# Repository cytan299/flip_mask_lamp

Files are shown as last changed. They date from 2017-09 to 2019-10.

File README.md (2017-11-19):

# Remote controlled flip Bahtinov mask and lamp

by C.Y. Tan 2017

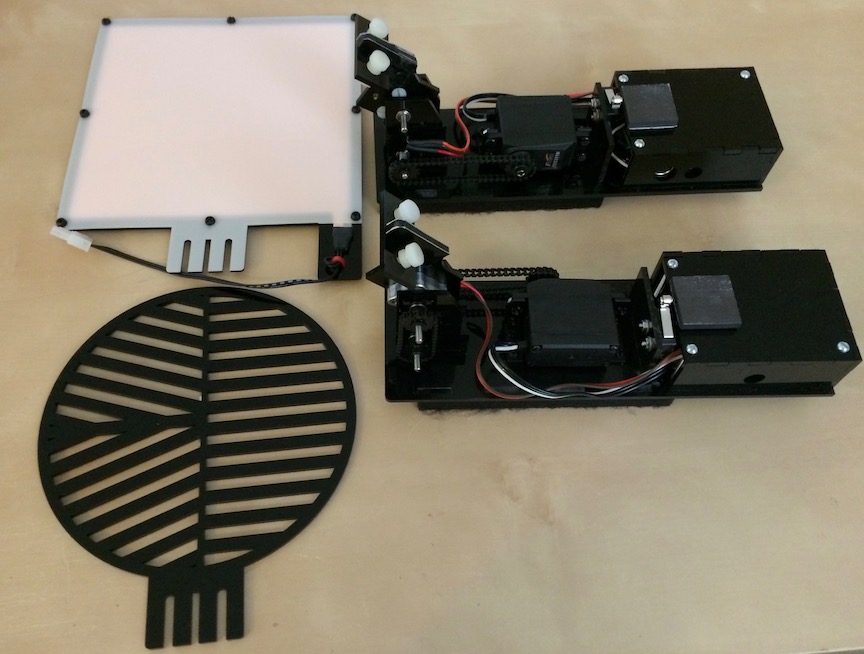
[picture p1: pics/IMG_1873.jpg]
Flip mask and lamp


I made a flip mask and lamp for my FSQ106 so that when they are
mounted on the telescope, they will balance each other out when mounted on
the opposite side of the telescope.

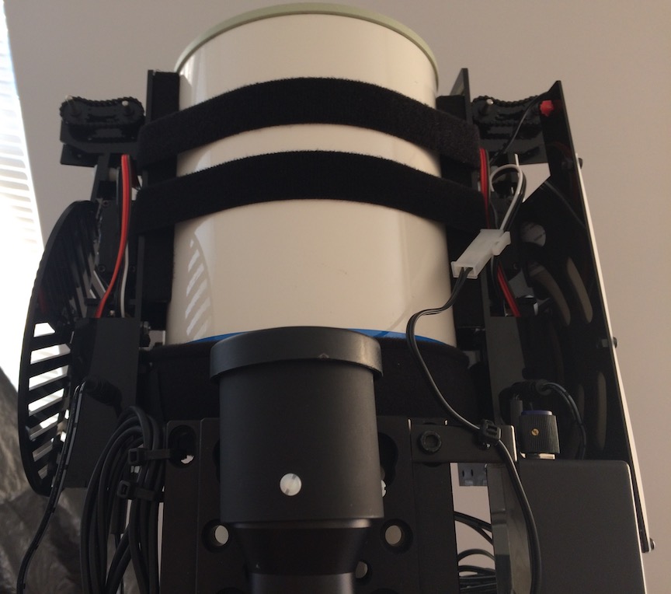
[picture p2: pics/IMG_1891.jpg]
Flip mask and lamp mounted on an FSQ106


## Design

The flip mask and lamp are designed as a master and slave pair. I have
chosen the flip mask controller to be the master and the flip lamp
controller to be the slave.

The mechanical design of the flip mask and lamp are mirror images of
each other. The principal parts used in the design are as follows:

* A servo controller made by Pololu called the [Maestro](https://www.pololu.com/product/1350).
* A servo that rotates greater than 270
degrees: the [Feetech FR5311M](http://www.feetechrc.com/product/continuous-rotation-servo/two-working-mode-digital-programmable-metal-gears-servo-fr5311m/).
* A [sprocket and chain system](https://www.servocity.com/0-1227-pitch-nylon-servo-sprockets) for connecting the servo to the mask and lamp.
* Interlock switches to indicate where the mask or lamp is
  * A mechanical lever switch
  * A Hall switch
* A lamp made from an
[electroluminescent panel with dimmer and power inverter](https://knema.com/collections/electroluminescent-el-panels/products/electroluminescent-panel-split-electrode-type-blue-green-or-white-includes-power-supply-and-dimmi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).
* Filter sheets have been added so that the RGB components of the EL panel have nearly
  the same intensities.

## Movie

A movie of how the flip mask and lamp in action can be found on [youtube](https://youtu.be/KrSrh4rIldk).

## Support

This is unsupported hardware. Build at your own peril! :)

You can submit questions or bug reports using the
[issues](https://github.com/cytan299/flip_mask_lamp/issues) tab on
the right and then click on **NEW**.

Have fun!

## Directory structure

* **howto** Assembly instructions for the flip mask and lamp.
* **ponoko** The files that are used for laser cutting the acrylic parts of
the design. These files can be sent directly to
[Ponoko](http://www.ponoko.com) for laser cutting.
* **bom** Bill of materials for 1 pair of flip mask and lamp.
* **eagle** Eagle schematic and board files.
* **python** Source code for the python control program.
* **pics** Photographs used in the README's and Wiki.

## Other information

More information can be found in he *README.md* files in each
directory and the [wiki](https://github.com/cytan299/flip_mask_lamp/wiki/Flip-Mask-and-Lamp) of this project on github.

## Copyright
All the software, documentation, and hardware that I have written is
copyright 2017 C.Y. Tan.

All software is released under GPLv3

All documentation is released under Creative Commons
Attribution-ShareAlike 3.0 Unported License or GNU Free
Documentation License, Version 1.3

All hardware is released under CERN Hardware Open License v1.2

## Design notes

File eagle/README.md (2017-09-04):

# Eagle files

These are the eagle files that can be sent to pc board manufacturers to
be made. There is a free version of [eagle](http://cadsoftusa.com)
that can be downloaded to view the designs.

## Directories

* **flip_mask** The flip mask control unit. This unit 
  * controls the Bahtinov mask
  * is the master that controls the flip lamp unit that is the slave unit
  * contains the USB interface
  * has the [Maestro](https://www.pololu.com/product/1350) servo controller
* **flip_lamp** The flip lamp control unit. This unit
  * controls the lamp

## Copyright

The schematic and board designs are copyright 2017 C.Y. Tan and
released under the CERN Open Hardware License v1.2

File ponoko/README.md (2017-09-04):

# Flip mask and lamp plastic parts

The flip mask and lamp plastic parts are in this directory. Note that
the svg files are *not* empty! The lines are 0.01 mm thick that are
required for laser cutting by [Ponoko](http://www.ponoko.com). To see
the designs, either zoom in or change the thickness of the lines with
a programme like [Inkscape](https://inkscape.org/en/).

* *flip_mask_and_lamp_ponoko_v2a.svg* contains enough parts for one pair
of flip mask and lamp parts. The remaining parts are sufficient for
either one flip mask or slave. The specified material used for manufacture at [Ponoko](http://www.ponoko.com) is
  * Black acrylic
  * 3.0 mm thick
  * P2 - 384.0 mm long x 384.0 mm wide
* *flip_lamp_front_ponoko_v2.svg* contains the design for the front of the lamp. The
material used is
  * White Delrin
  * 0.8 mm thick
  * P2 - 384.0 mm long x 384.0 mm wide
* *flip_lamp_back_ponoko_v2.svg*  contains the design for the back of the lamp. The
material used is
  * Black acrylic
  * 1.5 mm thick
  * P2 - 384.0 mm long x 384.0 mm wide

## Copyright

The flip mask and lamp design is copyright 2017 C.Y. Tan and released under the CERN Open Hardware License v1.2

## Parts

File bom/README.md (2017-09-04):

# Bill of Materials

The estimated cost for building *one* pair of flip mask and lamp is
about $400. Taxes and shipping have not been included. This is the
lower bound for the cost of one such device because, in practise, it
is not possible to just buy 1 screw.  The bom.ods file is readable
using [LibreOffice Calc](http://www.libreoffice.org).

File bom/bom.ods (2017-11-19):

Part # | Description | Price each | # required | Cost of 1 | Bought from | Total cost of 1
FR5311M | Digital Servo | $18.76 | 2 | $37.52 | www.robotshop.com | $417.71
RB-Fit-24 | Feetech FRS servo programmer | $4.99 | 1 | $4.99 | www.robotshop.com
RB-lyn-79 | Lynxmotion EZ aluminum servo mount | $8.95 | 1 | $8.95
C1227 | 1 foot 0.1227 plastic chain | $7.49 | 2 | $14.98 | www.servocity.com
FS154 | 15T, 25 spline servo teeth | $3.99 | 2 | $7.98
S152 | 15T press fit sprocket | $2.27 | 6 | $13.62
535036 | 1/8” ID, 1/4” OD flanged ball bearing | $1.40 | 8 | $11.16
634116 | 1/8” SS precision shafting 2” | $0.49 | 4 | $1.96
ROB-09664 | Micro Maestro 6-channel | $19.95 | 1 | $19.95 | www.sparkfun.com
ROB-12108 | Set screw hub – 1/8” bore | $4.99 | 2 | $9.98
EL8006 | Parallel electrode 6”x6” dimming EL panel with dimming controller and PS | $69.25 | 1 | $69.25 | www.knema.com
102-2705-ND | DCDC converter CUINC P7805-Q24-S5 | $4.94 | 1 | $4.94 | www.digikey.com
2144690 | 2.1 mm PCB mount power jack | $0.69 | 5 | $3.45
138202 | 0.0047uF, 50V cap | $0.15 | 2 | $0.30
1583041 | Solid state relay LCA710 | $4.49 | 1 | $4.49
46341 | 74LS05 | $0.79 | 1 | $0.79
119475 | 6 pin mini DIN socket female | $0.89 | 2 | $1.78
100766 | Female contact crimp pin | $0.19 | 12 | $2.28
303562 | Mini-fit female 2 position receptacle | $0.25 | 1 | $0.25
881004 | Mini-fit vertical male 2 position receptacle | $0.25 | 1 | $0.25
401824 | Mini-fit male contacts | $0.09 | 2 | $0.18
401701 | Mini-fit female contacts | $0.09 | 2 | $0.18
2096763 | 2.1 mm with 6 ft pigtail | $1.95 | 3 | $5.85
100280 | 24 awg 2 strand 100 ft | $9.95 | 0.03 | $0.30
2230352 | 14 pin IC socket | $0.49 | 1 | $0.49
167004 | 6 pin IC socket | $0.39 | 1 | $0.39
159599 | Roller action subminature switch | $1.35 | 2 | $2.70
158 | Hall effect sensor US5881LUA | $2.00 | 2 | $4.00 | www.adafruit.com
3141 | Female/female jumper wires | $2.95 | 1 | $2.95
3145 | Single row wire housing pack | $1.95 | 0.2 | $0.39
flip mask PCB | flip mask PCB | $8.67 | 1 | $8.67 | www.oshpark.com
flip lamp PCB | flip lamp PCB | $6.00 | 0 | $0.00
flip lamp PCB v2 | flip lamp PCB v2 | $6.00 | 1 | $6.00
308938 | flip mask, flip lamp front, flip lamp back | $95.76 | 1 | $95.76 | www.ponoko.com
30699202874 | Corner brace 1.5” black | $0.75 | 2 | $1.49 | www.homedepot.com
887480029215 | Machine screws and nuts 2-56 1/2” | $0.15 | 4 | $0.59
30699370115 | Machine screws and nuts 2-56 3/8” | $0.15 | 2 | $0.30
887480029215 | Machine screws and nuts 6-32 3/8” | $0.15 | 8 | $1.18
887480029918 | Machine screws and nuts 4-40 1.5” | $0.30 | 6 | $1.77
75967907006 | 7/8”*23 velcro straps | $1.32 | 2 | $2.65
302370993711 | 3ft DIN6 M to M cable | $1.99 | 1 | $1.99 | PJAJ Inc (ebay)
B01EIY7YKW | 150 M2-M5 nylon screws + nuts | $4.76 | 1 | $4.76 | Sodial® (amazon.com)
 | 160 M3 8 sizes nylon screws + nuts | $8.99 | 1 | $8.99 | GoChange (amazon.com)
147777 | Soft bendable aluminium tubes (3/32,1/8, 5/32) | $2.32 | 1 | $2.32 | www.hobbylobby.com
1025816 | Plast-I-weld | $7.99 | 1 | $7.99
 | Craft power magnets | $5.99 | 0 | $0.00
 | Square magnets with foam adhesive | $0.37 | 2 | $0.75
 | Galvanized steel sheet | $3.99 | 1 | $3.99
 | Black felt sheet | $3.99 | 1 | $3.99
D12-N52 | 1/16” dia x 1/8” thick magnet | $0.14 | 2 | $0.28 | www.kjmagnetics.com (http://www.kjmagnetics.com/proddetail.asp?prod=D12-N52)
R40 | Roscolux 40 (Light Salmon) | $6.99 | 1 | $6.99 | www.stagelightingstore.com
R07 | Roscolux 07 (Pale Yellow) | $6.99 | 1 | $6.99
R37 | Roscolux 37 (Pale Rose Pink) | $6.99 | 1 | $6.99
R365 | Roscolux 365 (Tharon Delft Blue) | $6.99 | 1 | $6.99

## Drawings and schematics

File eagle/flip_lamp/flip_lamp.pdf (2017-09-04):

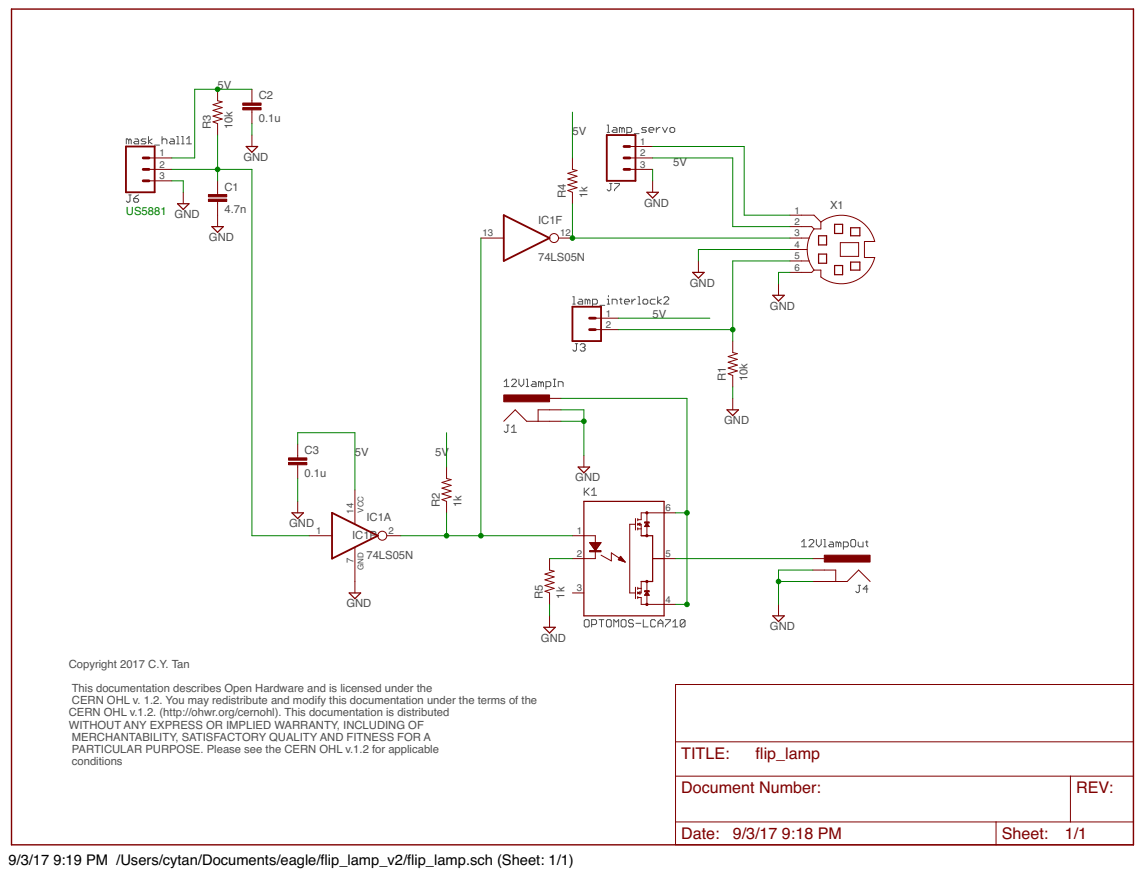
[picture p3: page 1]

Copyright 2017 C.Y. Tan This documentation describes Open Hardware and is licensed under the CERN OHL v. 1.2. You may redistribute and modify this documentation under the terms of the CERN OHL v.1.2. (http://ohwr.org/cernohl). This documentation is distributed

WITHOUT ANY EXPRESS OR IMPLIED WARRANTY, INCLUDING OF
MERCHANTABILITY, SATISFACTORY QUALITY AND FITNESS FOR A
PARTICULAR PURPOSE. Please see the CERN OHL v.1.2 for applicable
conditions

Document Number: | REV:

Date: 9/3/17 9:18 PM | Sheet: 1/1

9/3/17 9:19 PM /Users/cytan/Documents/eagle/flip_lamp_v2/flip_lamp.sch (Sheet: 1/1)

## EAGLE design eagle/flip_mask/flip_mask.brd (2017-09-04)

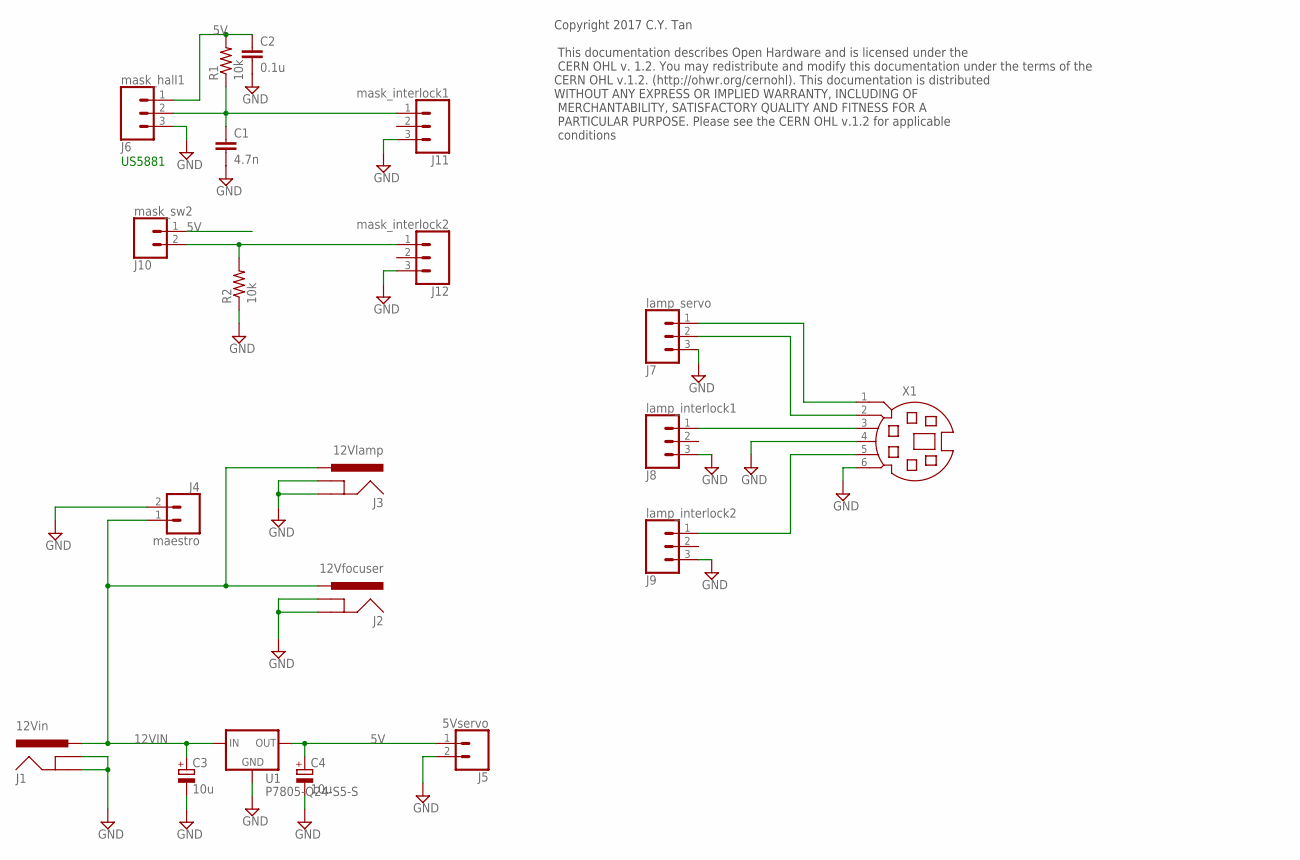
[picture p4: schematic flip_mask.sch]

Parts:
C1: 4.7n; CAP-PTH-5MM
C2: 0.1u; CAP-PTH-5MM
C3, C4: 10u; E2,5-6
J1: 12Vin; POWER_JACK_PTH
J2: 12Vfocuser; POWER_JACK_PTH
J3: 12Vlamp; POWER_JACK_PTH
J4: maestro; 1X02
J5: 5Vservo; 1X02
J6: mask_hall1; 1X03
J7: lamp_servo; 1X03
J8: lamp_interlock1; 1X03
J9: lamp_interlock2; 1X03
J10: mask_sw2; 1X02
J11: mask_interlock1; 1X03
J12: mask_interlock2; 1X03
R1, R2: 10k; 0207/10
U1: P7805-Q24-S5-S; DC-DC_CONVERTER_78XX
X1: MD06SS; MDIN06SS

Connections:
5V: C2.1, C4.+, J5.1, J6.1, J10.1, R1.2, U1.VOUT (OUT)
12VIN: C3.+, J1.PWR, J2.PWR, J3.PWR, J4.1, U1.VIN (IN)
GND: C1.2, C2.2, C3.-, C4.-, J1.GND, J1.GNDBREAK, J2.GND, J2.GNDBREAK, J3.GND, J3.GNDBREAK, J4.2, J5.2, J6.3, J7.3, J8.3, J9.3, J11.3, J12.3, R2.1, U1.GND, X1.4, X1.6
unnamed: C1.1, J6.2, J11.1, R1.1
unnamed: J7.2, X1.2
unnamed: J8.1, X1.3
unnamed: J10.2, J12.1, R2.2
unnamed: J7.1, X1.1
unnamed: J9.1, X1.5

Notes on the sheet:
US5881
Copyright 2017 C.Y. Tan This documentation describes Open Hardware and is licensed under the CERN OHL v. 1.2. You may redistribute and modify this documentation under the terms of the CERN OHL v.1.2. (http://ohwr.org/cernohl). This documentation is distributed WITHOUT ANY EXPRESS OR IMPLIED WARRANT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

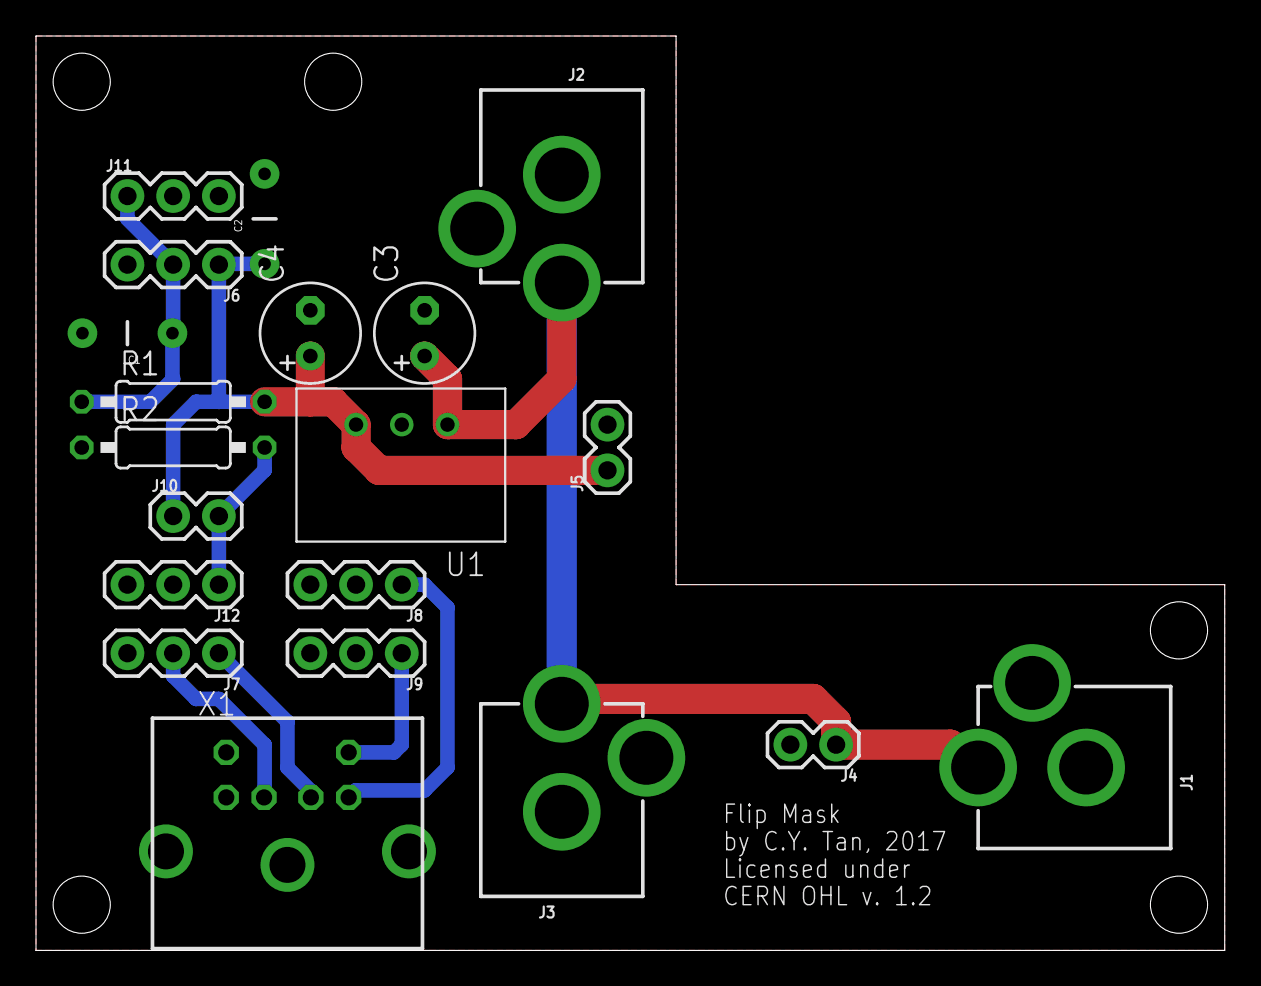
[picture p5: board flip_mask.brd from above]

Board: 2 copper layers, 66.0 x 50.8 mm, 20 parts (0 on the bottom side), 9 nets.

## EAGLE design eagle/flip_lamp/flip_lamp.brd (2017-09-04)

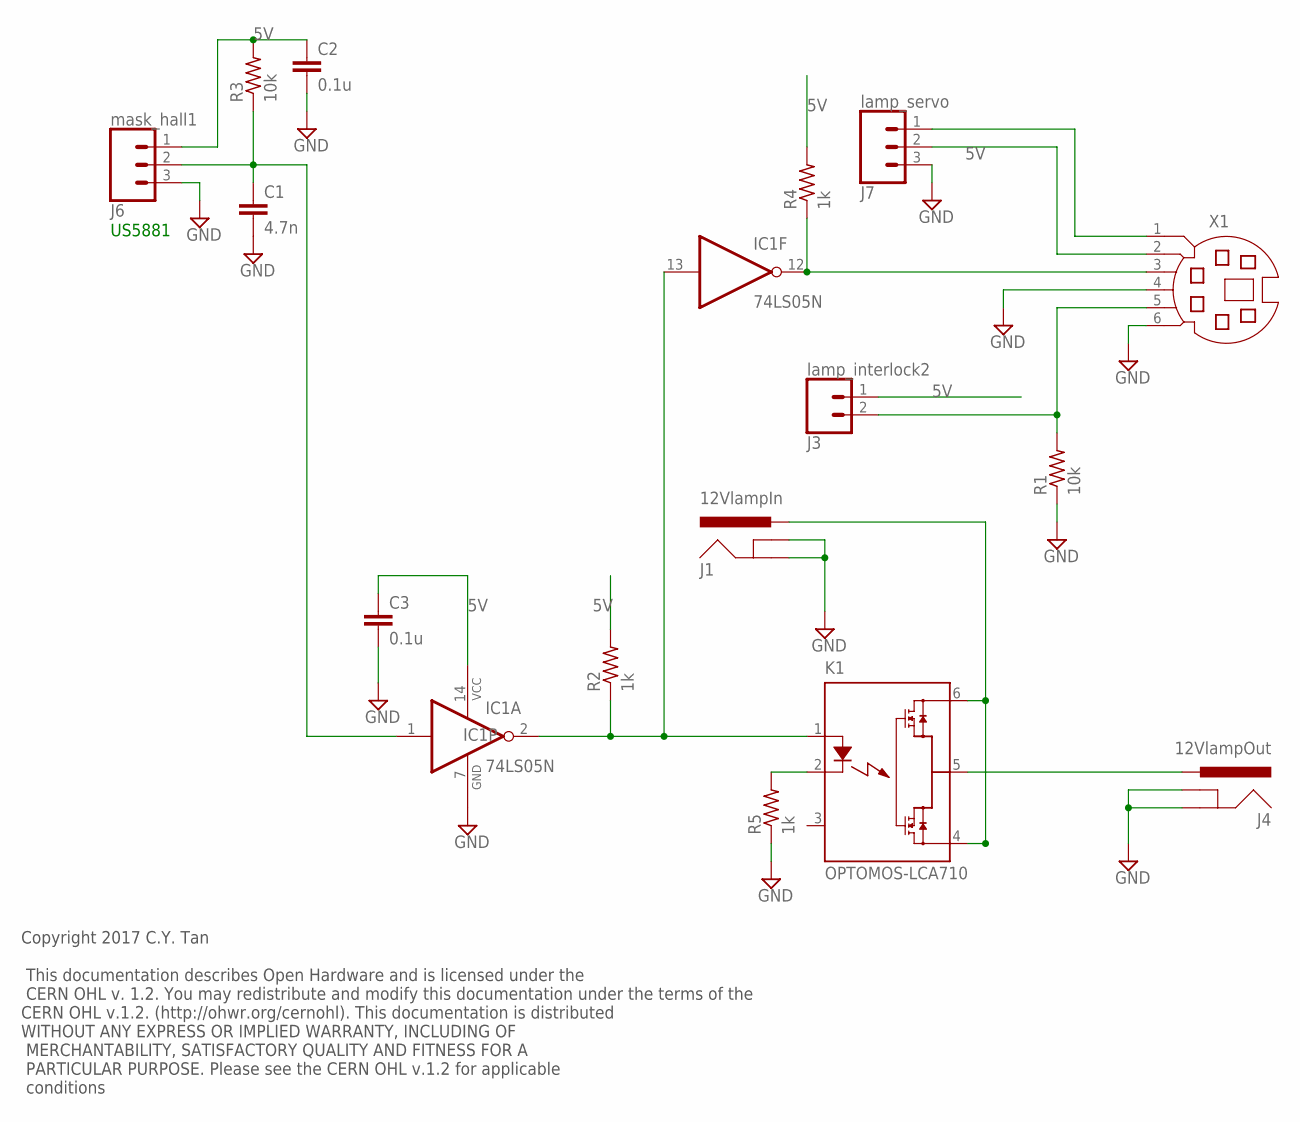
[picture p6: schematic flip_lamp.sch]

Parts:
C1: 4.7n; CAP-PTH-5MM
C2, C3: 0.1u; CAP-PTH-5MM
IC1: 74LS05N; DIL14
J1: 12VlampIn; POWER_JACK_PTH
J3: lamp_interlock2; 1X02
J4: 12VlampOut; POWER_JACK_PTH
J6: mask_hall1; 1X03
J7: lamp_servo; 1X03
K1: OPTOMOS-LCA710; DIL6
R1, R3: 10k; 0207/10
R2, R4, R5: 1k; 0207/10
X1: MD06SS; MDIN06SS

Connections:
5V: C2.1, C3.1, IC1.14 (VCC), J3.1, J6.1, J7.2, R2.2, R3.2, R4.2, X1.2
GND: C1.2, C2.2, C3.2, IC1.7 (GND), J1.GND, J1.GNDBREAK, J4.GND, J4.GNDBREAK, J6.3, J7.3, R1.1, R5.1, X1.4, X1.6
unnamed: IC1.12 (O), R4.1, X1.3
unnamed: J1.PWR, K1.4 (DS3), K1.6 (DS1)
unnamed: J4.PWR, K1.5 (DS2)
unnamed: IC1.2 (O), IC1.13 (I), K1.1 (A), R2.1
unnamed: J7.1, X1.1
unnamed: J3.2, R1.2, X1.5
unnamed: K1.2 (K), R5.2
unnamed: C1.1, IC1.1 (I), J6.2, R3.1

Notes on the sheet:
US5881
Copyright 2017 C.Y. Tan This documentation describes Open Hardware and is licensed under the CERN OHL v. 1.2. You may redistribute and modify this documentation under the terms of the CERN OHL v.1.2. (http://ohwr.org/cernohl). This documentation is distributed WITHOUT ANY EXPRESS OR IMPLIED WARRANT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

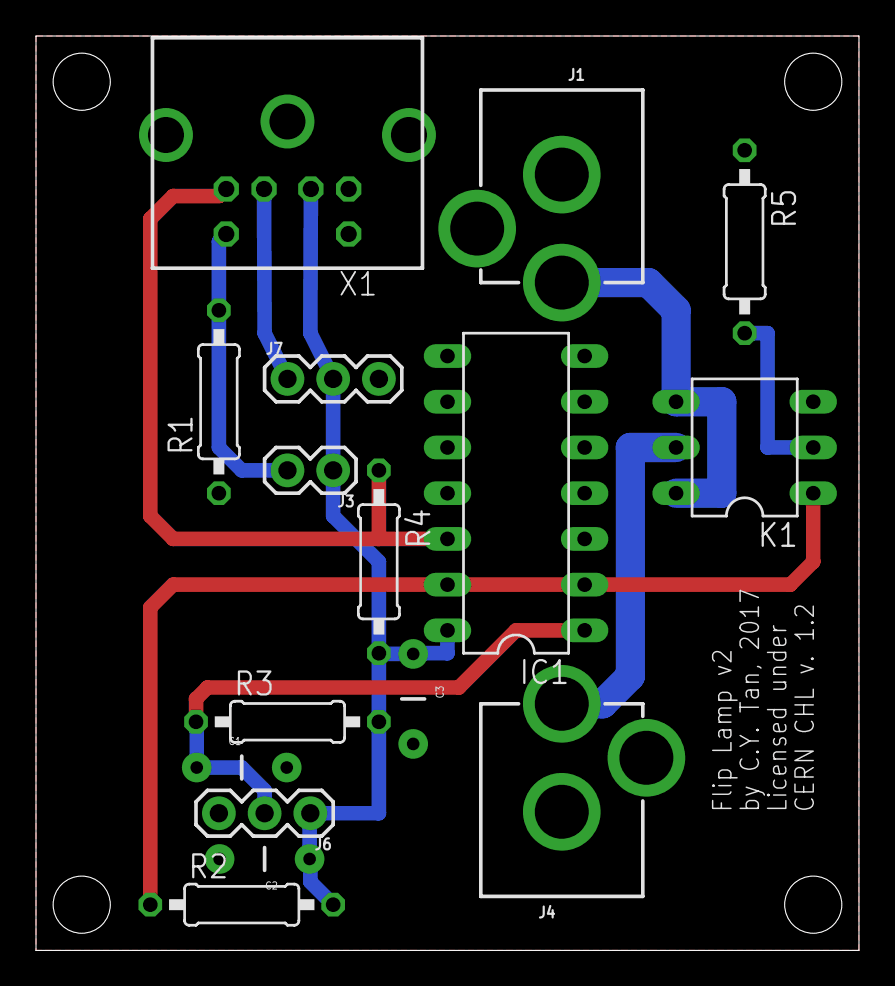
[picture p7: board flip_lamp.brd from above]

Board: 2 copper layers, 45.7 x 50.8 mm, 16 parts (0 on the bottom side), 10 nets.

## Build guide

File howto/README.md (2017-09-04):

# How to build the flip mask and lamp

I have written these one documents to help you build and assemble a
flip mask and lamp

## The document

* **assembly.pdf** This guide highlights the important steps for
  assembling the flip mask and lamp.

## Copyright

These documents are copyright 2017 C.Y. Tan and released under
Creative Commons Attribution-ShareAlike 3.0 Unported License.

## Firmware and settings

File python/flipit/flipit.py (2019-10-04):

"""
    flipit.py is the python script for controlling flip_mask and flip_lamp
    Copyright (C) 2017  C.Y. Tan
    Contact: cytan299@yahoo.com

    This file is part of flipit.py

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
    You should have received a copy of the GNU General Public License
    along with derot.  If not, see <http://www.gnu.org/licenses/>.
"""
__author__ = "C.Y. Tan"
__copyright__ = "Copyright 2017, C.Y. Tan"
__credits__ = [""]
__license__ = "GPL"
__version__ = "0.1"
__maintainer__ = "C.Y. Tan"
__email__ = "cytan299@yahoo.com"
__status__ = "alpha"

import time;

import os;
import platform;

import argparse;

from maestro import Controller;
import serial; # import again to get exceptions

#######################################################
# Initialization code
#######################################################

if (platform.uname()[0] == "Darwin"):
  SERIAL_PORT="/dev/cu.usbmodem00183281";
  # define the clear screen command depending on OS
  CLEAR_SCREEN = "clear";

if(platform.uname()[0] == "Windows"):  
  SERIAL_PORT="COM3";
  # define the clear screen command depending on OS
  CLEAR_SCREEN = "cls";

# constants

FLIP_MASK=0; # servo channel of flip mask
FLIP_LAMP=1; # servo channel of flip lamp

CH_MASK_ON = 2; # Hall probe channel that indicates mask is on
CH_MASK_OFF = 3; # interlock channel for the mask when it is off

CH_LAMP_ON = 4; # Hall probe channel that indicates lamp is on
CH_LAMP_OFF = 5; # interlock channel for the lamp when it is off

# set the speed of the servo so that the mask and lamp doesn't
# flip too quickly
MASK_SERVO_SPEED = 40; # 40*0.25us/10 ms= 10 us change per 10 ms. OR 1 ms/s.
LAMP_SERVO_SPEED = 40;

# set the acceleration of the servos. 0 unrestricted. 1 is slowest. 
# Range is 0 to 255
MASK_SERVO_ACCEL = 2;
LAMP_SERVO_ACCEL = 1;

# flip mask target values
FLIP_MASK_ON=500; # us
FLIP_MASK_NEUTRAL=1500;
FLIP_MASK_OFF=3200;

# flip lamp target values
FLIP_LAMP_ON=2400; #us
FLIP_LAMP_NEUTRAL=1500;
FLIP_LAMP_OFF=400;

# do nothing value is negative
DO_NOTHING=-1;

########################################################
# menu() - prints out the menu options for the user to select
########################################################
def menu():
    print("Flip options:");
    print("\tMask\t\tLamp");
    print("\t 1: OFF\t\t 7: OFF");
    print("\t 2: ON\t\t 8: ON");
    print("\t 3: Neutral\t 9: Neutral");
    print("\t 0: exit");
    print("=> ", end="");
    return int(input());

########################################################
# is_mask_on(): returns true if mask is in "on" position
########################################################
def is_mask_on(servo):
  if servo.getPosition(CH_MASK_ON) < 128:
    return True;
  else:
    return False;
  

########################################################
# is_mask_off(): returns true if mask is "off" position
########################################################

def is_mask_off(servo):
  if servo.getPosition(CH_MASK_OFF) > 512:
    return True;
  else:
    return False;

########################################################
# is_lamp_on(servo): returns true if lamp is in "on" position
########################################################
def is_lamp_on(servo):
  if servo.getPosition(CH_LAMP_ON) < 128:
    return True;
  else:
    return False;

########################################################
# is_lamp_off(): returns true if lamp is in "off" position
########################################################

def is_lamp_off(servo):
  if servo.getPosition(CH_LAMP_OFF) > 512:
    return True;
  else:
    return False;

########################################################
# print_state() - prints out the current state of the flip mask and lamp
########################################################
def print_state(servo):
  print("**************************");
  print("Mask: ", end="");
  if is_mask_on(servo):
    print("ON", end="");
  elif is_mask_off(servo):
    print("OFF", end="");
  else:
    print("?", end="");

  print("\t Lamp: ", end="");
  if is_lamp_on(servo):
    print("ON", end="");
  elif is_lamp_off(servo):
    print("OFF", end="");
  else:
    print("?", end="");

  print("");
  print("**************************");  
    

########################################################
# main entry point
########################################################

# parse any commandline arguments
parser = argparse.ArgumentParser(description="flip mask and lamp control programme");

if (platform.uname()[0] == "Darwin"):
  parser.add_argument("serial_port", type=str, nargs='?', default=SERIAL_PORT, help='serial port name. Default: '+ SERIAL_PORT);

if(platform.uname()[0] == "Windows"):  
  parser.add_argument("serial_port", type=str, nargs='?', default=SERIAL_PORT, help='serial port name. Default: ' + SERIAL_PORT);
args = parser.parse_args();

# completed parsing the commandline arguments and let's open the serial port etc.
try:
  servo = Controller(args.serial_port);
except serial.SerialException:
  print("flipit.py: cannot open ", args.serial_port);
  exit();

servo.setSpeed(FLIP_MASK, MASK_SERVO_SPEED);
servo.setAccel(FLIP_MASK, MASK_SERVO_ACCEL);
servo.setSpeed(FLIP_LAMP, LAMP_SERVO_SPEED);
servo.setAccel(FLIP_LAMP, LAMP_SERVO_ACCEL);

# for some stupid reason the above speeds and accelerations
# don't seem to be executed until the first command is sent
servo.setTarget(FLIP_MASK, FLIP_MASK_OFF*4);
servo.setTarget(FLIP_LAMP, FLIP_LAMP_OFF*4);

# Print out the current state of the flip mask and lamp
_=os.system(CLEAR_SCREEN);
print_state(servo);

# Now we can process the user inputs
while 1:
  choice = menu();

  print("Working ...");

  if choice == 0:
    servo.close();
    _=os.system(CLEAR_SCREEN);
    exit();
  if choice == 1:
    target = FLIP_MASK_OFF;
  elif choice == 2:
    # check that the lamp is already on. If so, do nothing
    if is_lamp_on(servo):
      choice = DO_NOTHING;
    target = FLIP_MASK_ON;
  elif choice == 3:
    target = FLIP_MASK_NEUTRAL;
  elif choice == 7:
    target = FLIP_LAMP_OFF;
  elif choice == 8:
    # check that the mask is already on. If so, do nothing
    if is_mask_on(servo): 
      choice = DO_NOTHING;  
    target = FLIP_LAMP_ON;
  elif choice == 9:
    target = FLIP_LAMP_NEUTRAL;

  if choice < 0:
    if target == FLIP_MASK_ON:
       print("!!!! Error: FLIP LAMP is still on !!!!");
    if target == FLIP_LAMP_ON:
       print("!!!! Error: FLIP MASK is still on !!!!");
  else:  
    if 1<= choice <= 3: 
      servo.setTarget(FLIP_MASK, target*4);
    if 7<= choice <=9:
      servo.setTarget(FLIP_LAMP, target*4);

    time.sleep(5.0);
    _=os.system(CLEAR_SCREEN);
    print_state(servo);

          

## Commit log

2017-09-04 First commit of flip mask and lamp
    [bom.ods, flip_lamp.brd, flip_lamp.sch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]
2017-11-19 Added instructions in assembly.pdf and updated the bill of materials bom.ods for filter sheets.
    [bom.ods]
2019-10-04 removed and re-added python/flipit subdirectory so that python files are in repo
    [flipit.py]

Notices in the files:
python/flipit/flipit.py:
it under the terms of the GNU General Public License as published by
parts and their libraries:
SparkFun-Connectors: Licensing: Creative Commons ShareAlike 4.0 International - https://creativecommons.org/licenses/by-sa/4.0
